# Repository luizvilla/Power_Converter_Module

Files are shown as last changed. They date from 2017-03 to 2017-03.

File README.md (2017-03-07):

# Power_Converter_Module
This repository holds an open-hardware Power Converter Module

Copyright LAAS 2016

This documentation describes Open Hardware and is licensed under the
CERN OHL v. 1.2.

You may redistribute and modify this documentation under the terms of the
CERN OHL v.1.2. (http://ohwr.org/cernohl). This documentation is distributed
WITHOUT ANY EXPRESS OR IMPLIED WARRANTY, INCLUDING OF
MERCHANTABILITY, SATISFACTORY QUALITY AND FITNESS FOR A
PARTICULAR PURPOSE. Please see the CERN OHL v.1.2 for applicable
conditions

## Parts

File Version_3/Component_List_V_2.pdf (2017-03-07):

COMPONENT LIST - DC/DC CONVERTER
Block | Id | Designator | Package | Qty | Designation | Sld.
Support | | P1,P2,P3,P4 | Plastic screws | 4 | -
| | N1,N2,N3,N4 | Plastic nuts | 4 | -
| | M1,M2,M3,M4 | Metal spacers | 4 | -

Driver

1 | DD1 | Diode DO-41 SOD81 Horizontal RM10 | 1 | DIODE
2 | ROH1,ROH2 | Resistor_Horizontal_RM10mm | 2 | 330
3 | CD3 | C_Rect_L7_W2_P5 | 1 | 500n
4 | DR1 | DIP-14_W7.62mm_LongPads | 1 | IRS2186
5 | JPO1,JPO2,JPO3,JPO4 | Pin_Header_Straight_1x02 | 4 | JUMPER
6 | OPT1 | DIP-8_W7.62mm_LongPads | 1 | TLP2631
7 | RM1,RM2 | Resistor_Horizontal_RM10mm | 2 | 2R2
8 | RO1,RO2 | Resistor_Horizontal_RM10mm | 2 | 470
9 | RO3,RO4 | Resistor_Horizontal_RM10mm | 2 | 220
10 | CO1 | C_Rect_L7_W2_P5_fat | 1 | C
11 | CD2,CD1 | C_Rect_L7_W2_P5_fat | 2 | 100n

Feeder

12 | FH2 | 7805 | 1 | 7815
13 | CONH1,CONL1 | BARREL_JACK | 2 BARREL_JACK
14 | DH1,DH2,DL1 | Diode_DO-41_SOD81_Horizontal_RM10 3 | D_Small
15 | FH1,FL1 | 7805 | 2 | 7805
16 | JPF1 | Pin_Header_Straight_1x03 | 1 | JUMPER3
17 | LDH1,LDH2,LDL1 | LED-3MM | 3 | LED
18 | RH1,RH2,RL1 | Resistor_Horizontal_RM10mm | 3 | 10k
19 | CL2,CL1,CH4,CH3,CH2,CH1 | C_Rect_L7_W2_P5_fat | 6 | 1u
20 | PVH1,PVL1 | Potentiometer | 2 | 1M
21 | RiH1,RiL1 | Resistor_TO-220_Vertical | 2 | 0.02
22 | RVH1,RVL1 | Resistor_Horizontal_RM10mm | 2 | 470k
23 | RVH2,RVL2 | Resistor_Horizontal_RM10mm | 2 | 4k7
24 | iA3,iA1,iA2,iA4 | AMC1100 | 4 | AMC1100
25 | C_Rect_L7_W2_P5_fat | 8 | 100nF
Micro | 26 | SH_1,SH2 | ARDUINO_SHIELD_2 | 2

Power

27 | CNH1 | Banana_Jack_2Pin | 1 | HIGH
28 | CNL1 | Banana_Jack_2Pin | 1 | LOW
29 | CPH1,CPL1 | C_Radial_D12.5_L25_P5 | 2 | C
30 | MH1,ML1 | TO-220 | 2 | FDPF39N20
31 | CNDbH1,CNDb1 | Pin_Header_Angled_2x08 | 2 CONN_02X08
32 | L1 | MURATA_Inductor_Big | 1 | INDUCTOR

Measure
ment

C_M8,C_M7,C_M6,C_M5,C_M4,C_ M3,C_M2,C_M1
ARDUINO_SHI
ELD

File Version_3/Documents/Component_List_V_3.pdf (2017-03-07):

COMPONENT LIST - DC/DC CONVERTER
Block | Id | Designator | Package | Qty | Designation
Support | | P1,P2,P3,P4 N1,N2,N3,N4 | Plastic screws Plastic nuts | 4 4 | --
Driver | 1 2 3 4 5 6 7 8 9 10 11 | DD1 ROH1,ROH2 CD3 DR1 JPO1,JPO2,JPO3,JPO4 OPT1 RM1,RM2 RO1,RO2 RO3,RO4 CO1 CD2,CD1 | Diode DO-41 SOD81 Horizontal RM10 Resistor_Horizontal_RM10mm C_Rect_L7_W2_P5 DIP-14_W7.62mm_LongPads Pin_Header_Straight_1x02 DIP-8_W7.62mm_LongPads Resistor_Horizontal_RM10mm Resistor_Horizontal_RM10mm Resistor_Horizontal_RM10mm C_Rect_L7_W2_P5_fat C_Rect_L7_W2_P5_fat | 1 2 1 1 4 1 2 2 2 1 2 | 1N4007 330 500n IRS2186 JUMPER TLP2631 2R2 470 220 100n 100n
Feeder | 12 13 14 15 16 17 18 19 | FH2 CONH1,CONL1 DH1,DH2,DL1 FH1,FL1 JPF1 LDH1,LDH2,LDL1 RH1,RH2,RL1 CL2,CL1,CH4,CH3,CH2,C H1 | 7805 - TO-220 BARREL_JACK Diode_DO-41_SOD81_Horizontal_RM10 7815 - TO-220 Pin_Header_Straight_1x03 LED-3MM Resistor_Horizontal_RM10mm C_Rect_L7_W2_P5_fat | 1 2 3 2 1 3 3 6 | 7815 BARREL_JACK 1N4002 7805 JUMPER3 LED 10k 1u
Measurem ent | 20 21 22 23 24 25 | PVH1,PVL1 RiH1,RiL1 RVH1,RVL1 RVH2,RVL2 iA3,iA1,iA2,iA4 C_M8,C_M7,C_M6,C_M 5,C_M4,C_M3,C_M2,C_ M1 | Potentiometer Resistor_TO-220_Vertical Resistor_Horizontal_RM10mm Resistor_Horizontal_RM10mm AMC1100 C_Rect_L7_W2_P5_fat | 2 2 2 2 4 8 | 1M or 500k 0.02 470k 4k7 AMC1100 100nF
Micro | 26 | Ard_1 SH_1,SH2 | ARDUINO_UNO ARDUINO_SHIELD_2 | 1 2 | ARDUINO ARDUINO_SH IELD
Power | 27 28 29 30 32 | CNH1 CNL1 CPH1,CPL1 MH1,ML1 L1 | Banana_Jack_2Pin Banana_Jack_2Pin C_Radial_D12.5_L25_P5 TO-220 MURATA_Inductor_Big | 1 1 2 2 1 | HIGH LOW C FDPF39N20 INDUCTOR

Debug

33 | P_Test | Borne_test_noir | 14 | T_?
34 | P_Test | Borne_test_rouge | 14 | T_?
PCB | 35 | PCB | PCB | 10 | PCB
Other | 35 | Consummables | - | 1 | -

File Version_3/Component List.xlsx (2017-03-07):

COMPONENT LIST - DC/DC CONVERTER
Block | Id | Designator | Package | Qty | Designation | Sld.
Debug | 1 | TH1,TH2,TH3,TH4,TH5,TH6,TH7,TH8,TH9,TH10,TH11,TH12,TH13,TH14,TH15,TH16,TL1,TL2,TL3,TL4,TL5,TL6,TL7,TL8,TL9,TL10,TL11,TL12 | Measurement_Point_Round-TH_Small | 28 | CONN_01X01
 | 2 | CNDb1 | Pin_Header_Angled_2x08 | 1 | CONN_02X08
 | 3 | SH_1,SH2 | ARDUINO_SHIELD_2 | 2 | ARDUINO_SHIELD
Driver | 4 | DD1 | Diode DO-41 SOD81 Horizontal RM10 | 1 | DIODE
 | 5 | ROH1,ROH2 | Resistor_Horizontal_RM10mm | 2 | 330
 | 6 | CD3 | C_Rect_L7_W2_P5 | 1 | 500n
 | 7 | DR1 | DIP-14_W7.62mm_LongPads | 1 | IRS2186
 | 8 | JPO1,JPO2,JPO3,JPO4 | Pin_Header_Straight_1x02 | 4 | JUMPER
 | 9 | OPT1 | DIP-8_W7.62mm_LongPads | 1 | TLP2631
 | 10 | RM1,RM2 | Resistor_Horizontal_RM10mm | 2 | 2R2
 | 11 | RO1,RO2 | Resistor_Horizontal_RM10mm | 2 | 470
 | 12 | RO3,RO4 | Resistor_Horizontal_RM10mm | 2 | 220
 | 13 | CO1 | C_Rect_L7_W2_P5_fat | 1 | C
 | 14 | C_M8,C_M7,C_M6,C_M5,C_M4,C_M3,C_M2,C_M1 | C_Rect_L7_W2_P5_fat | 8 | 100nF
 | 15 | CD2,CD1 | C_Rect_L7_W2_P5_fat | 2 | 100n
Feeder | 16 | FH2 | 7805 | 1 | 7815
 | 17 | CONH1,CONL1 | BARREL_JACK | 2 | BARREL_JACK
 | 18 | DH1,DH2,DL1 | Diode_DO-41_SOD81_Horizontal_RM10 | 3 | D_Small
 | 19 | FH1,FL1 | 7805 | 2 | 7805
 | 20 | JPF1 | Pin_Header_Straight_1x03 | 1 | JUMPER3
 | 21 | LDH1,LDH2,LDL1 | LED-3MM | 3 | LED
 | 22 | RH1,RH2,RL1 | Resistor_Horizontal_RM10mm | 3 | 10k
 | 23 | CL2,CL1,CH4,CH3,CH2,CH1 | C_Rect_L7_W2_P5_fat | 6 | 1u
Measurement | 24 | PVH1,PVL1 | Potentiometer | 2 | 1M
 | 25 | RiH1,RiL1 | Resistor_TO-220_Vertical | 2 | 0.02
 | 26 | RVH1,RVL1 | Resistor_Horizontal_RM10mm | 2 | 470k
 | 27 | RVH2,RVL2 | Resistor_Horizontal_RM10mm | 2 | 4k7
 | 28 | iA3,iA1,iA2,iA4 | AMC1100 | 4 | AMC1100
Micro | 29 | SH_1,SH2 | ARDUINO_SHIELD_2 | 2 | ARDUINO_SHIELD
Power | 30 | CNH1 | Banana_Jack_2Pin | 1 | HIGH
 | 31 | CNL1 | Banana_Jack_2Pin | 1 | LOW
 | 32 | CPH1,CPL1 | C_Radial_D12.5_L25_P5 | 2 | C
 | 33 | MH1,ML1 | TO-220 | 2 | FDPF39N20
 | 34 | CNDbH1,CNDb1 | Pin_Header_Angled_2x08 | 2 | CONN_02X08
 | 35 | L1 | MURATA_Inductor_Big | 1 | INDUCTOR

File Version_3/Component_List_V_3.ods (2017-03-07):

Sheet: Resumé
Dépense | Description | Valeur
Composants | Tout les composants nécessaires | 700,00 €
Cartes | 6 PCBs | 300,00 €
Consommables | Papier et autres | 50,00 €
 | Total | 1 050,00 €
 | Total par carte | 175,00 €

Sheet: Détails
COMPONENT LIST - DC/DC CONVERTER |  |  |  |  |  | Costs
Block | Id | Designator | Package | Qty | Designation | Price unit | Number | Sub-total
Support |  | P1,P2,P3,P4 | Plastic screws | 4 | - | 10,000 € | 1 | 10,00 €
 |  | N1,N2,N3,N4 | Plastic nuts | 4 | - | 10,000 € | 1 | 10,00 €
Driver | 1 | DD1 | Diode DO-41 SOD81 Horizontal RM10 | 1 | 1N4007 | 0,050 € | 100 | 5,00 €
 | 2 | ROH1,ROH2 | Resistor_Horizontal_RM10mm | 2 | 330 | 0,050 € | 20 | 1,00 €
 | 3 | CD3 | C_Rect_L7_W2_P5 | 1 | 500n | 0,500 € | 20 | 10,00 €
 | 4 | DR1 | DIP-14_W7.62mm_LongPads | 1 | IRS2186 | 0,000 € | 1 | 0,00 €
 | 5 | JPO1,JPO2,JPO3,JPO4 | Pin_Header_Straight_1x02 | 4 | JUMPER | 0,500 € | 6 | 3,00 €
 | 6 | OPT1 | DIP-8_W7.62mm_LongPads | 1 | TLP2631 | 1,500 € | 20 | 30,00 €
 | 7 | RM1,RM2 | Resistor_Horizontal_RM10mm | 2 | 2R2 | 0,055 € | 50 | 2,75 €
 | 8 | RO1,RO2 | Resistor_Horizontal_RM10mm | 2 | 470 | 0,042 € | 20 | 0,84 €
 | 9 | RO3,RO4 | Resistor_Horizontal_RM10mm | 2 | 220 | 0,050 € | 20 | 1,00 €
 | 10 | CO1 | C_Rect_L7_W2_P5_fat | 1 | 100n | 0,200 € | 20 | 4,00 €
 | 11 | CD2,CD1 | C_Rect_L7_W2_P5_fat | 2 | 100n | 0,200 € | 20 | 4,00 €
Feeder | 12 | FH2 | 7805 - TO-220 | 1 | 7815 | 0,300 € | 10 | 3,00 €
 | 13 | CONH1,CONL1 | BARREL_JACK | 2 | BARREL_JACK | 1,500 € | 20 | 30,00 €
 | 14 | DH1,DH2,DL1 | Diode_DO-41_SOD81_Horizontal_RM10 | 3 | 1N4002 | 0,050 € | 100 | 5,00 €
 | 15 | FH1,FL1 | 7815 - TO-220 | 2 | 7805 | 0,300 € | 20 | 6,00 €
 | 16 | JPF1 | Pin_Header_Straight_1x03 | 1 | JUMPER3 | 0,500 € | 6 | 3,00 €
 | 17 | LDH1,LDH2,LDL1 | LED-3MM | 3 | LED | 0,300 € | 30 | 9,00 €
 | 18 | RH1,RH2,RL1 | Resistor_Horizontal_RM10mm | 3 | 10k | 0,050 € | 30 | 1,50 €
 | 19 | CL2,CL1,CH4,CH3,CH2,CH1 | C_Rect_L7_W2_P5_fat | 6 | 1u | 0,500 € | 50 | 25,00 €
Measurement | 20 | PVH1,PVL1 | Potentiometer | 2 | 1M or 500k | 1,000 € | 20 | 20,00 €
 | 21 | RiH1,RiL1 | Resistor_TO-220_Vertical | 2 | 0.02 | 6,000 € | 15 | 90,00 €
 | 22 | RVH1,RVL1 | Resistor_Horizontal_RM10mm | 2 | 470k | 0,050 € | 20 | 1,00 €
 | 23 | RVH2,RVL2 | Resistor_Horizontal_RM10mm | 2 | 4k7 | 0,050 € | 20 | 1,00 €
 | 24 | iA3,iA1,iA2,iA4 | AMC1100 | 4 | AMC1100 | 3,060 € | 30 | 91,80 €
 | 25 | C_M8,C_M7,C_M6,C_M5,C_M4,C_M3,C_M2,C_M1 | C_Rect_L7_W2_P5_fat | 8 | 100nF | 0,200 € | 20 | 4,00 €
Micro |  | Ard_1 | ARDUINO_UNO | 1 | ARDUINO | 5,000 € | 6 | 30,00 €
 | 26 | SH_1,SH2 | ARDUINO_SHIELD_2 | 2 | ARDUINO_SHIELD | 2,000 € | 10 | 20,00 €
Power | 27 | CNH1 | Banana_Jack_2Pin | 1 | HIGH | 4,000 € | 6 | 24,00 €
 | 28 | CNL1 | Banana_Jack_2Pin | 1 | LOW | 4,000 € | 6 | 24,00 €
 | 29 | CPH1,CPL1 | C_Radial_D12.5_L25_P5 | 2 | C | 5,000 € | 20 | 100,00 €
 | 30 | MH1,ML1 | TO-220 | 2 | FDPF39N20 | 1,300 € | 30 | 39,00 €
 | 32 | L1 | MURATA_Inductor_Big | 1 | INDUCTOR | 10,000 € | 6 | 60,00 €
Debug | 33 | P_Test | Borne_test_noir | 14 | T_? | 0,200 € | 100 | 20,00 €
 | 34 | P_Test | Borne_test_rouge | 14 | T_? | 0,200 € | 100 | 20,00 €
PCB | 35 | PCB | PCB | 10 | PCB | 50,000 € | 6 | 300,00 €
Other | 35 | Consummables | - | 1 | - | 50,000 € | 1 | 50,00 €
 |  |  |  |  |  |  | TOTAL | 1 058,89 €
 |  |  |  |  |  |  | TOTAL PAR PCB | 176,48 €

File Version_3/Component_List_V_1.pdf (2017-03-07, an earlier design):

Block | Id | Designator | Package | Qty | Designation
Debug | 1 2 3 | TH1,TH2,TH3,TH4,TH5,TH6,T H7,TH8,TH9,TH10,TH11,TH1 2,TH13,TH14,TH15,TH16,TL1 ,TL2,TL3,TL4,TL5,TL6,TL7,TL8 ,TL9,TL10,TL11,TL12 CNDb1 SH_1,SH2 | Measurement_Point_Round-TH_Small Pin_Header_Angled_2x08 ARDUINO_SHIELD_2 | 28 1 2 | CONN_01X01 CONN_02X08 ARDUINO_SHIELD
Driver | 4 DD1 5 6 7 8 9 10 11 12 13 14 15 | ROH1,ROH2 CD3 DR1 JPO1,JPO2,JPO3,JPO4 OPT1 RM1,RM2 RO1,RO2 RO3,RO4 CO1 C_M8,C_M7,C_M6,C_M5,C_ M4,C_M3,C_M2,C_M1 CD2,CD1 | RM10 Resistor_Horizontal_RM10mm C_Rect_L7_W2_P5 DIP-14_W7.62mm_LongPads Pin_Header_Straight_1x02 DIP-8_W7.62mm_LongPads Resistor_Horizontal_RM10mm Resistor_Horizontal_RM10mm Resistor_Horizontal_RM10mm C_Rect_L7_W2_P5_fat C_Rect_L7_W2_P5_fat C_Rect_L7_W2_P5_fat | 1 DIODE 2 1 1 4 1 2 2 2 1 8 2 | R 500n IRS2186 JUMPER TLP2631 2R2 470 220 C 100nF 100n
Feeder | 17 18 DH1,DH2,DL1 19 20 21 22 23 24 | CONH1,CONL1 FH1,FL1 JPF1 LDH1,LDH2,LDL1 RH1,RH2,RL1 CL2,CL1,CH4,CH3,CH2,CH1 PVH1,PVL1 | BARREL_JACK Diode_DO-41_SOD81_Horizontal_RM10 7805 Pin_Header_Straight_1x03 LED-3MM Resistor_Horizontal_RM10mm C_Rect_L7_W2_P5_fat Potentiometer | 2 3 2 1 3 3 6 2 | BARREL_JACK D_Small 7805 JUMPER3 LED 10k 1u 1M
Measure ment | 25 26 27 28 | RiH1,RiL1 RVH1,RVL1 RVH2,RVL2 iA3,iA1,iA2,iA4 | Resistor_TO-220_Vertical Resistor_Horizontal_RM10mm Resistor_Horizontal_RM10mm AMC1100 | 2 2 2 4 | 0.02 470k 4k7 AMC1100
Micro | 29 30 | SH_1,SH2 CNH1 | ARDUINO_SHIELD_2 Banana_Jack_2Pin | 2 1 | ARDUINO_SHIELD HIGH
Power | 31 32 33 34 35 | CNL1 CPH1,CPL1 MH1,ML1 CNDbH1,CNDb1 L1 | Banana_Jack_2Pin C_Radial_D12.5_L25_P5 TO-220 Pin_Header_Angled_2x08 MURATA_Inductor_Big | 1 2 2 2 1 | LOW C FDPF39N20 CONN_02X08 INDUCTOR

Diode DO-41 SOD81 Horizontal

16 | FH2 | 7805 | 1 | 7815

COMPONENT LIST - DC/DC CONVERTER

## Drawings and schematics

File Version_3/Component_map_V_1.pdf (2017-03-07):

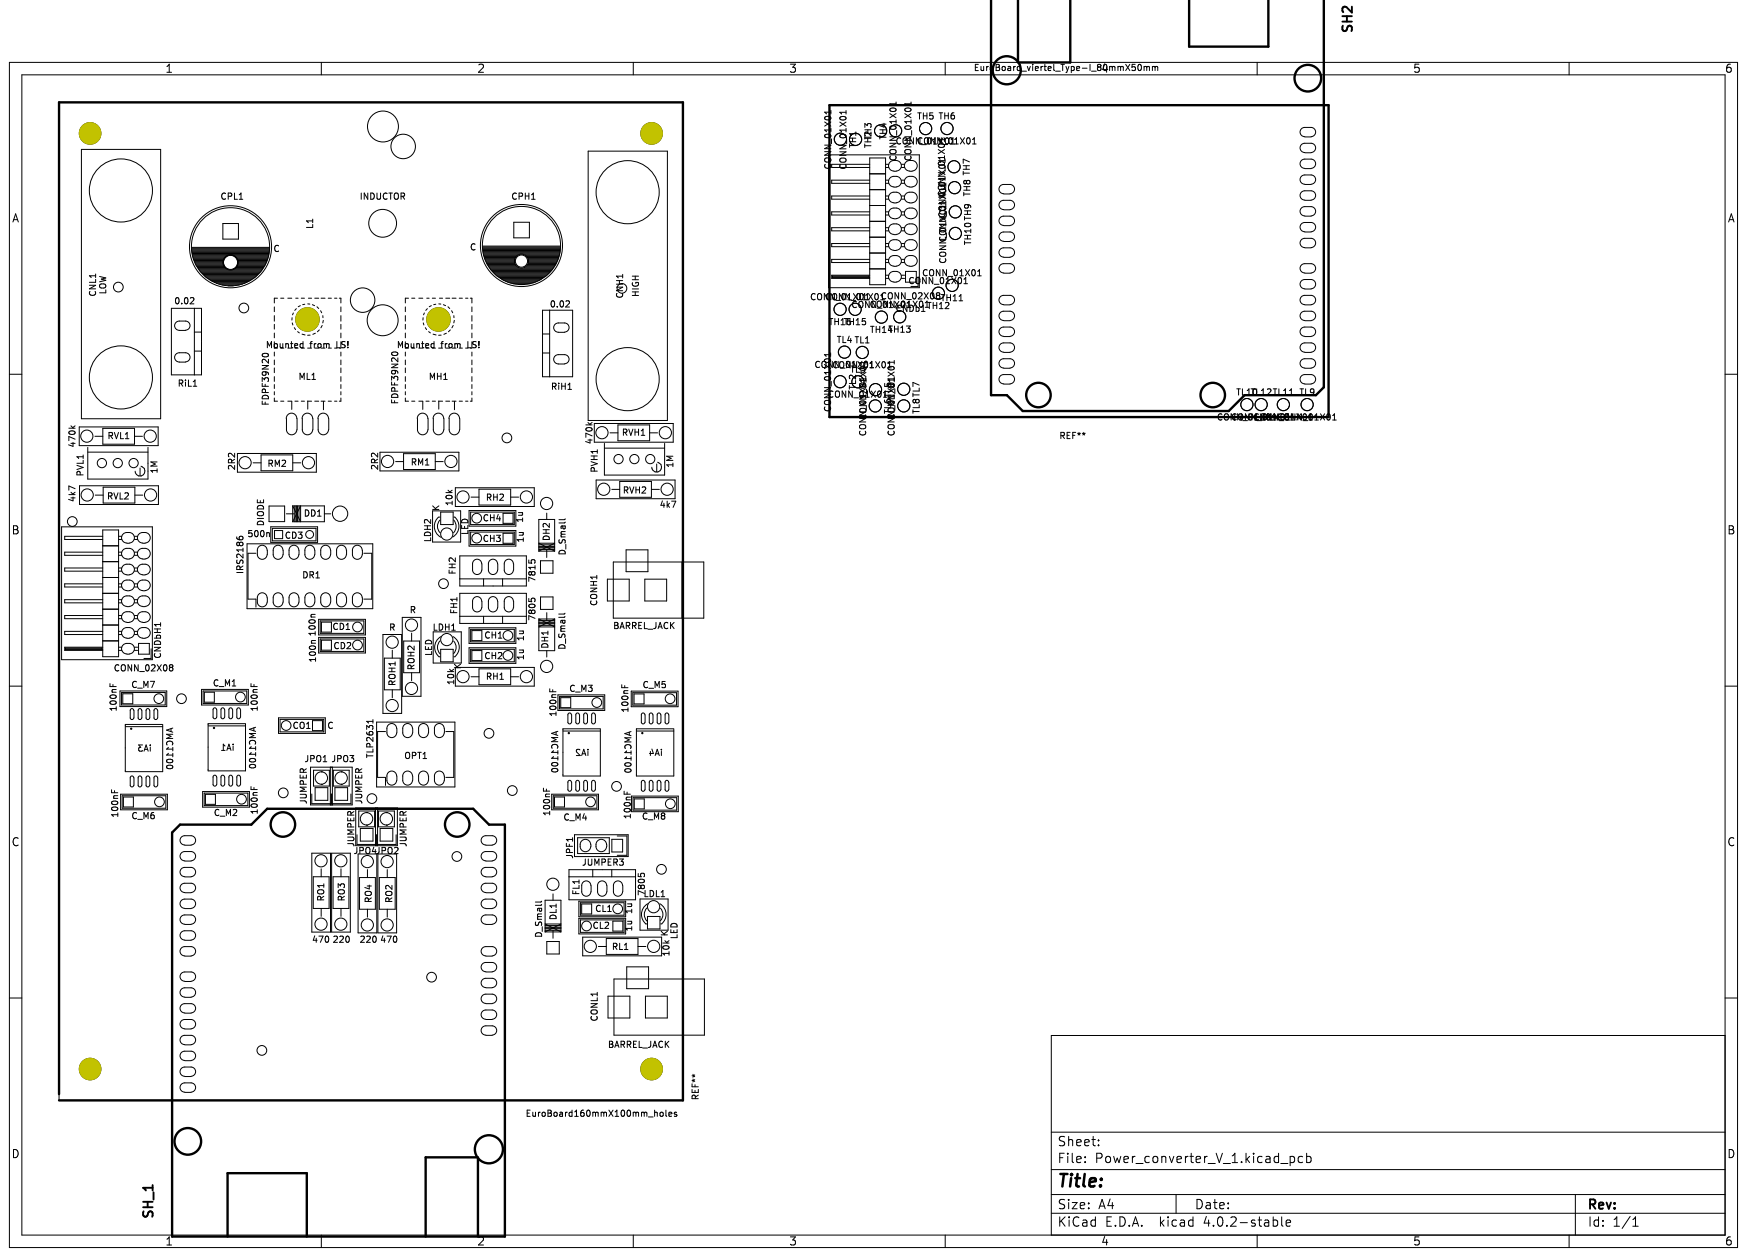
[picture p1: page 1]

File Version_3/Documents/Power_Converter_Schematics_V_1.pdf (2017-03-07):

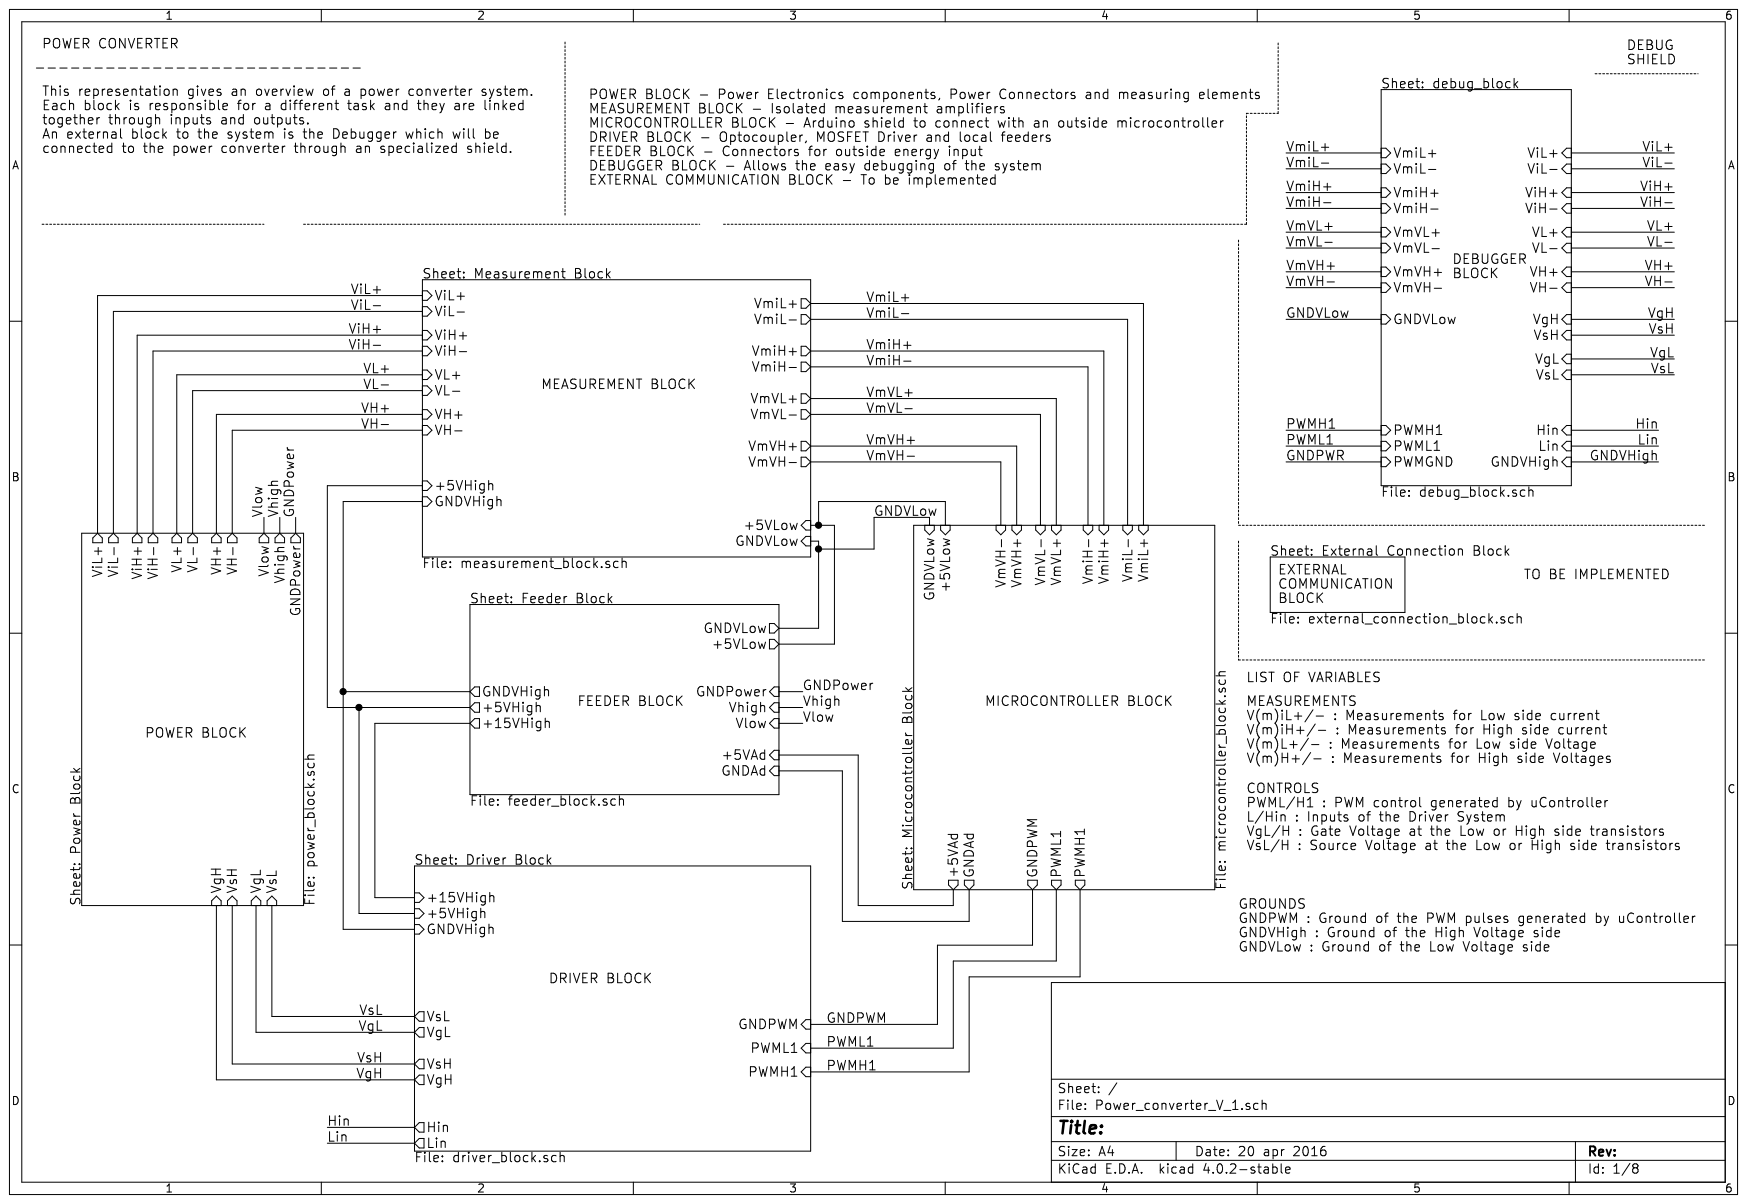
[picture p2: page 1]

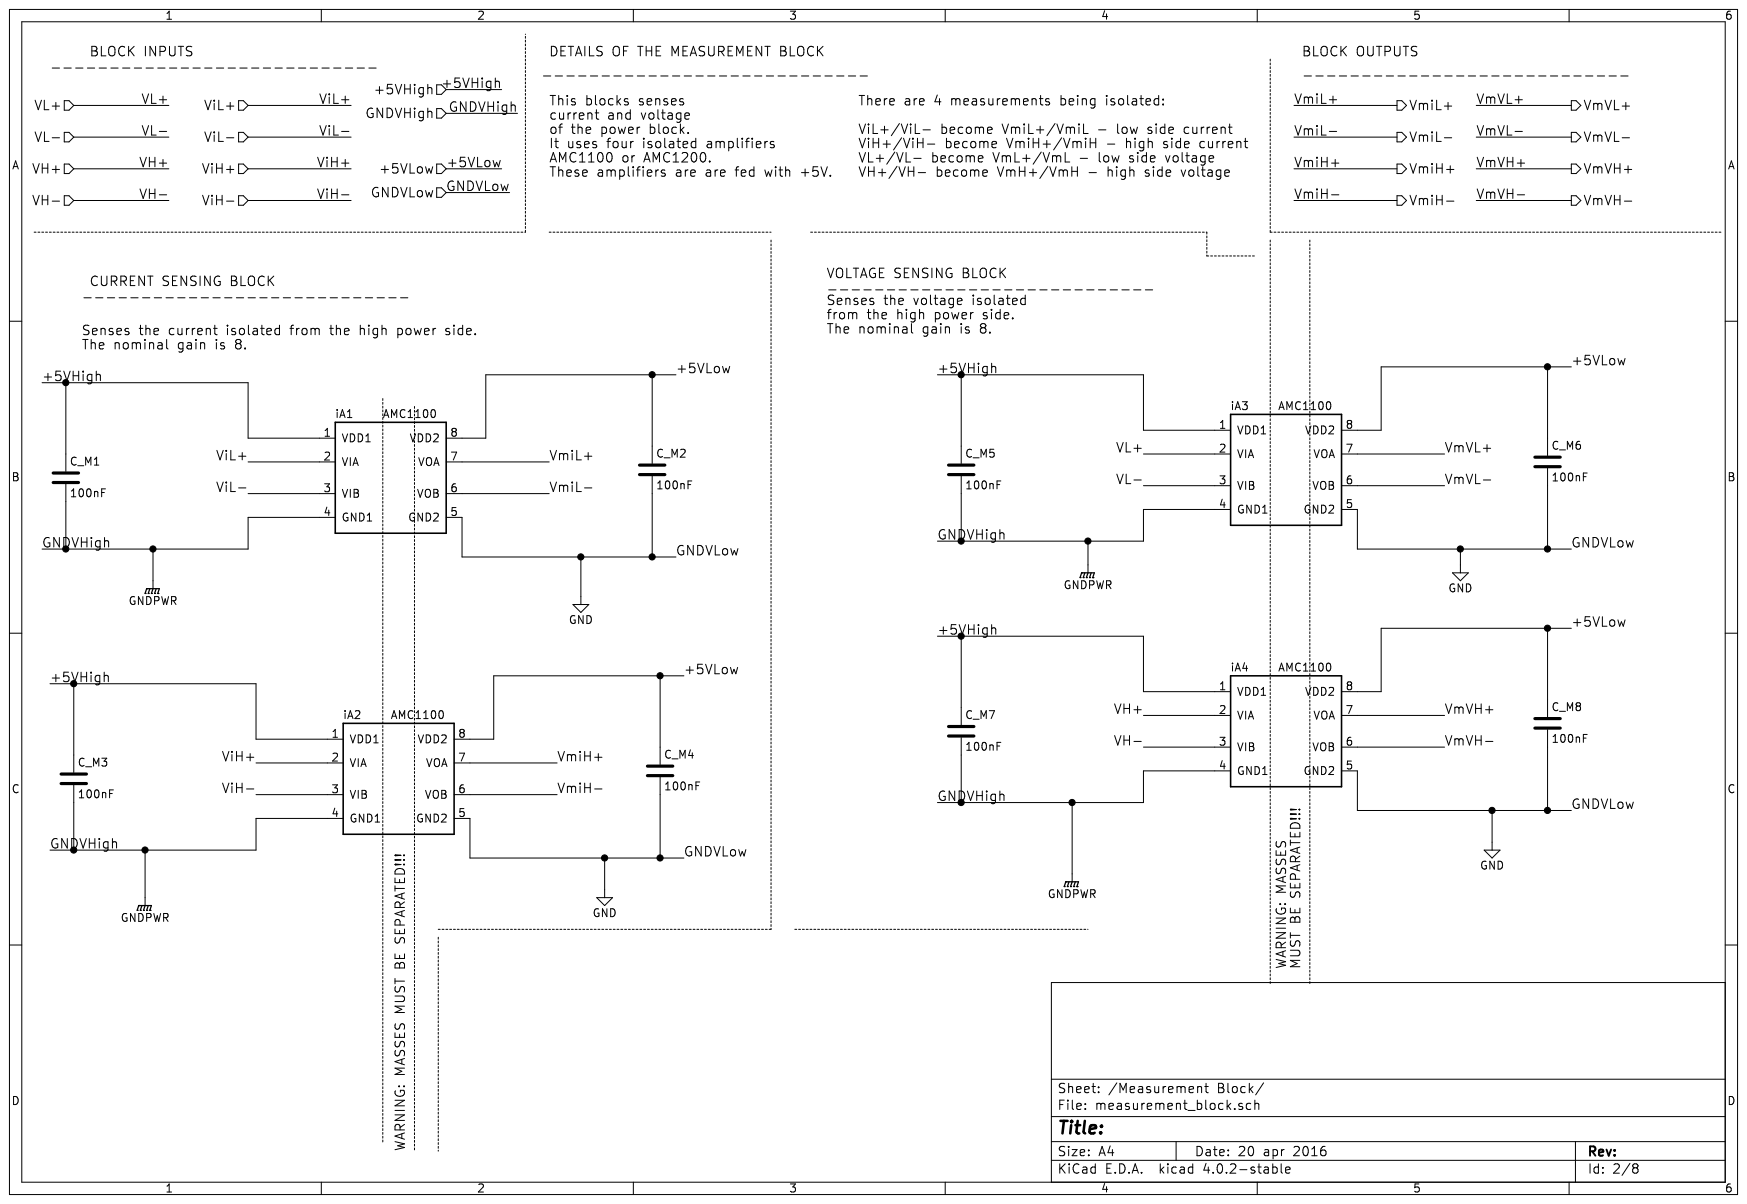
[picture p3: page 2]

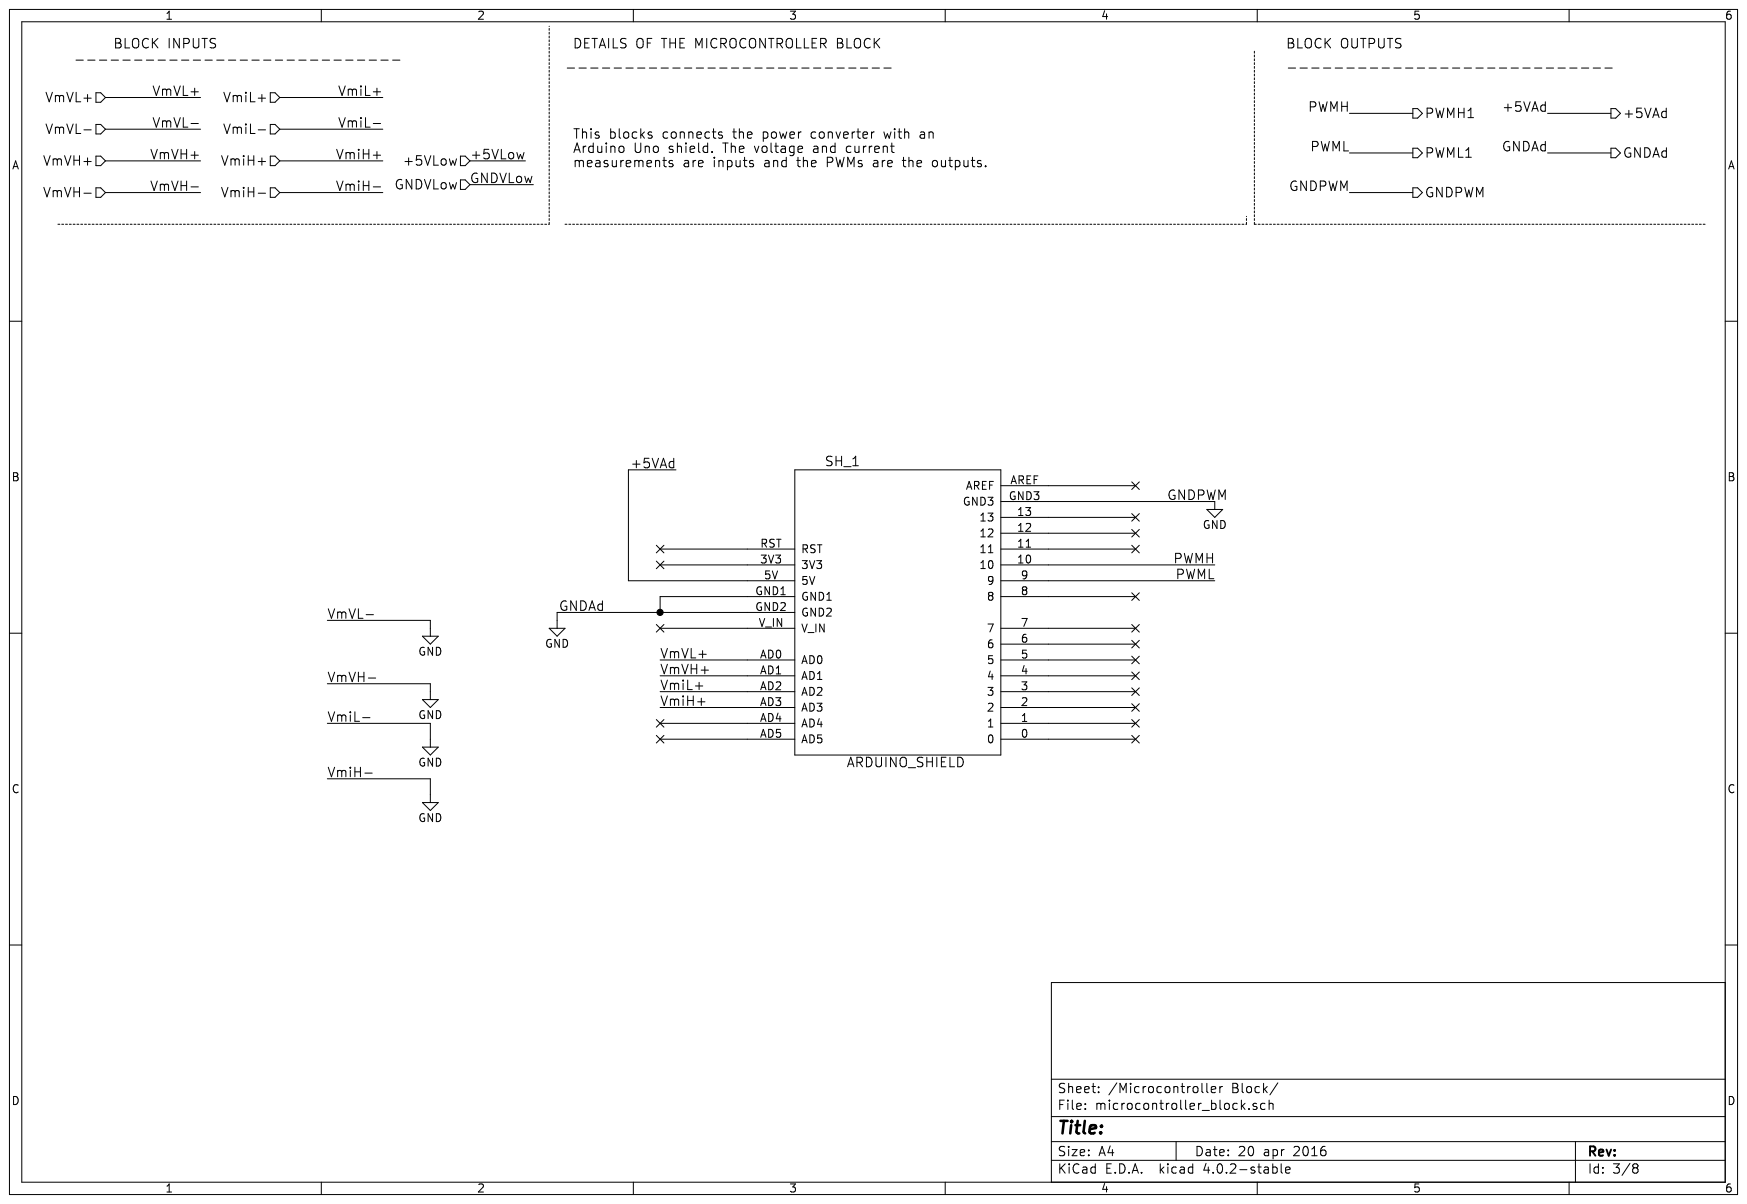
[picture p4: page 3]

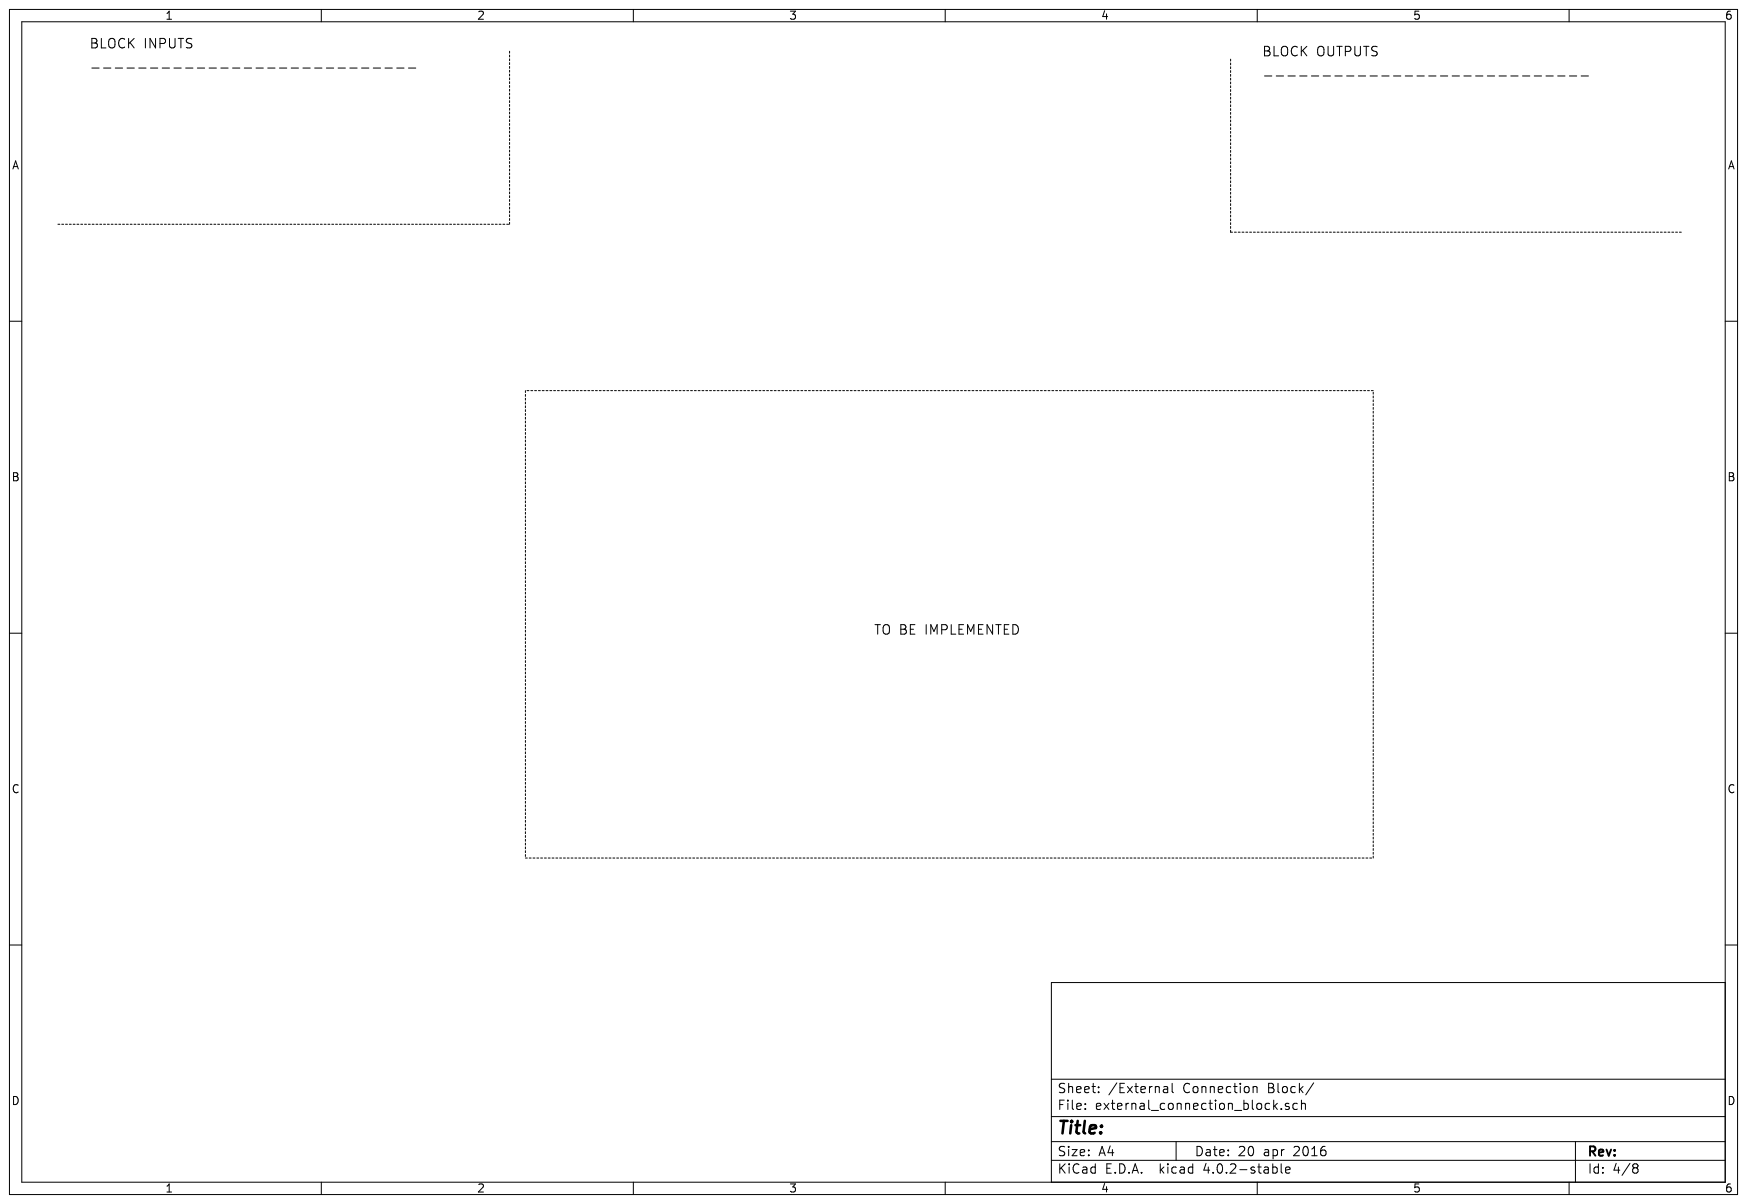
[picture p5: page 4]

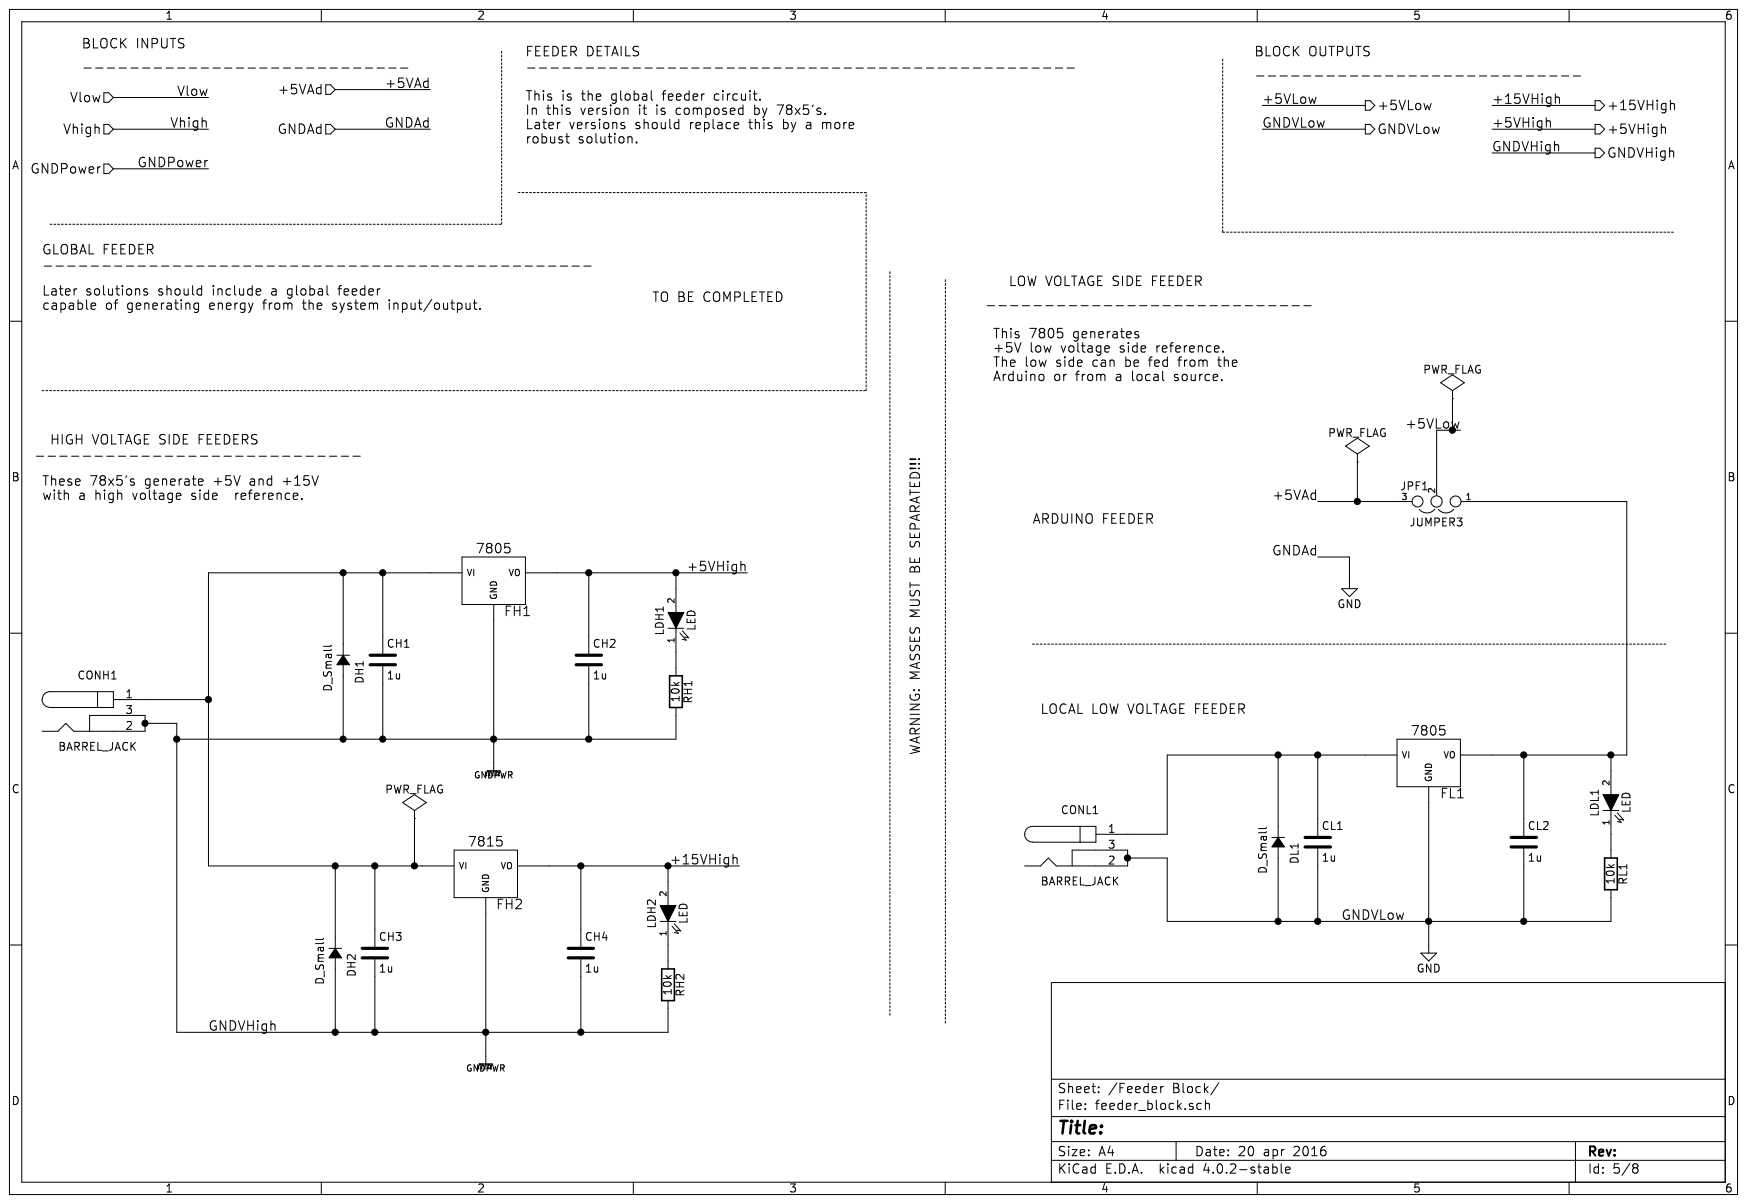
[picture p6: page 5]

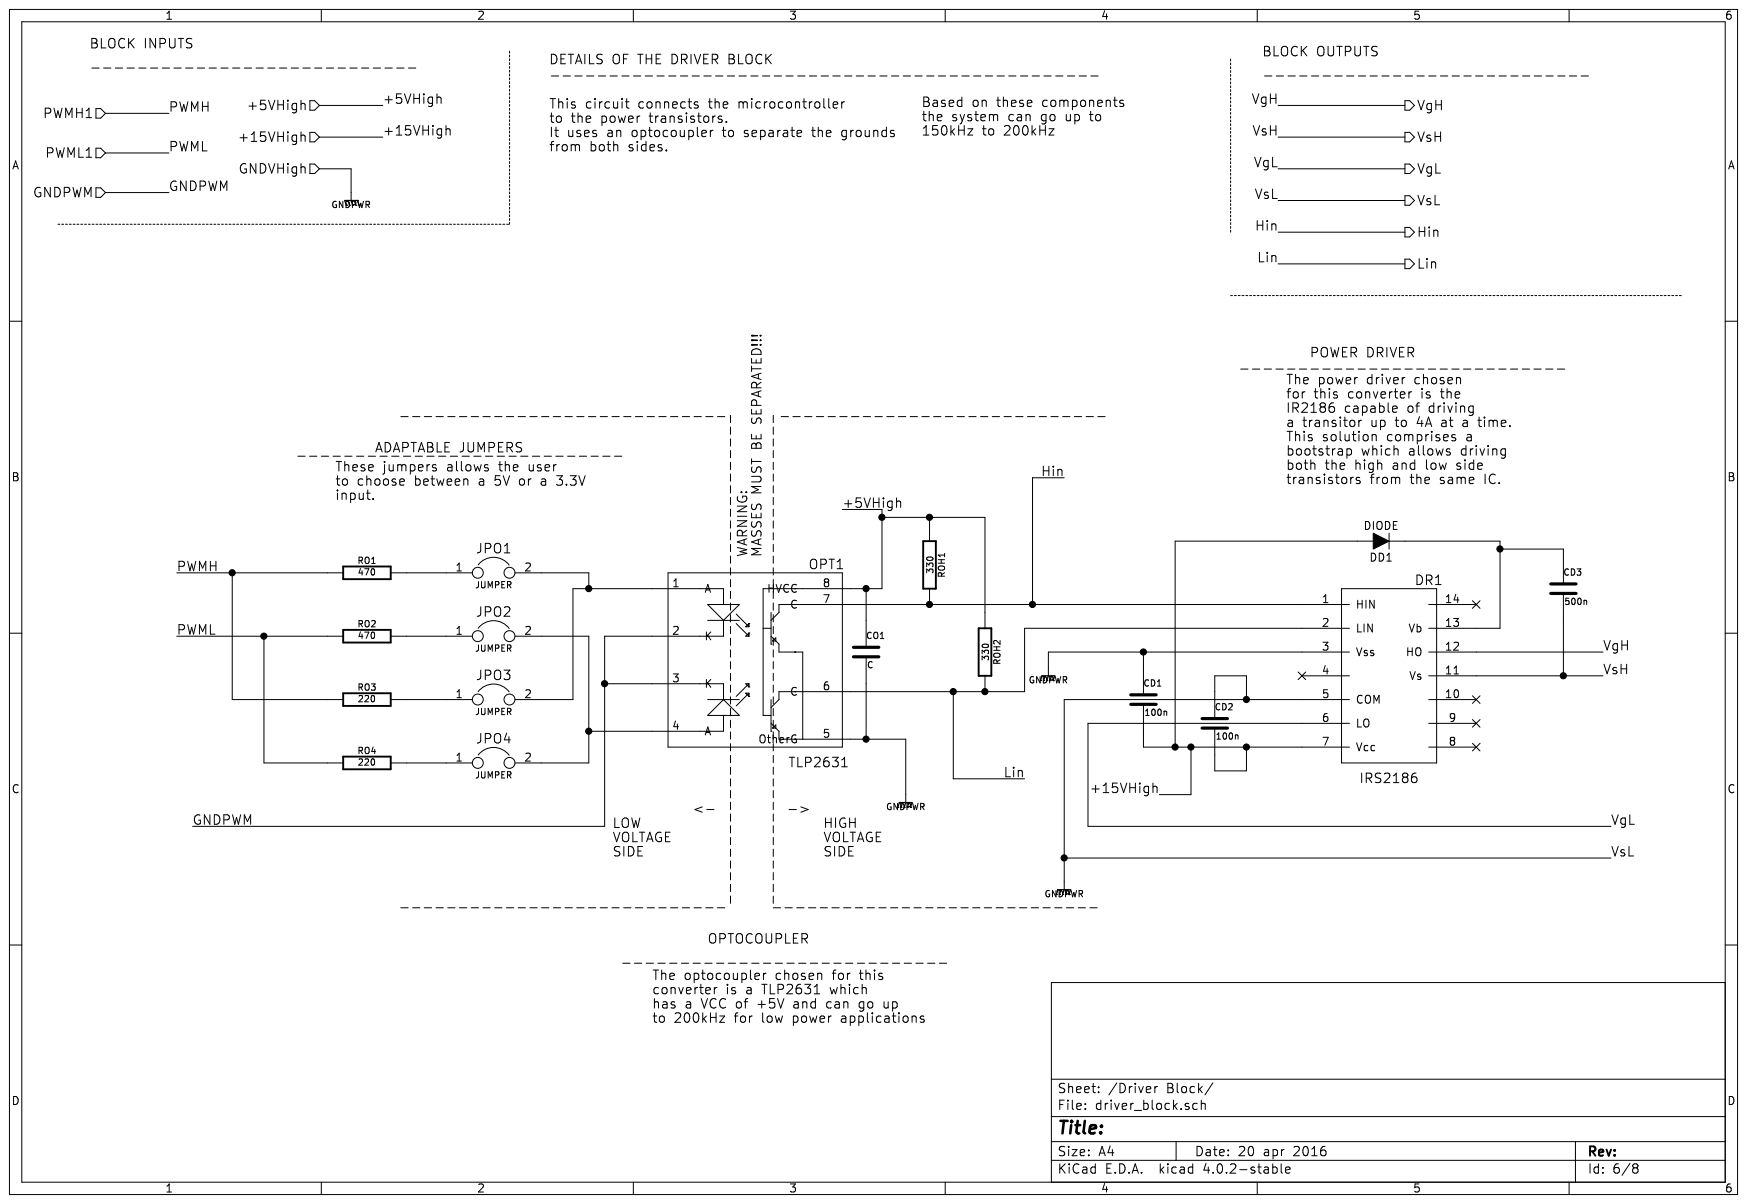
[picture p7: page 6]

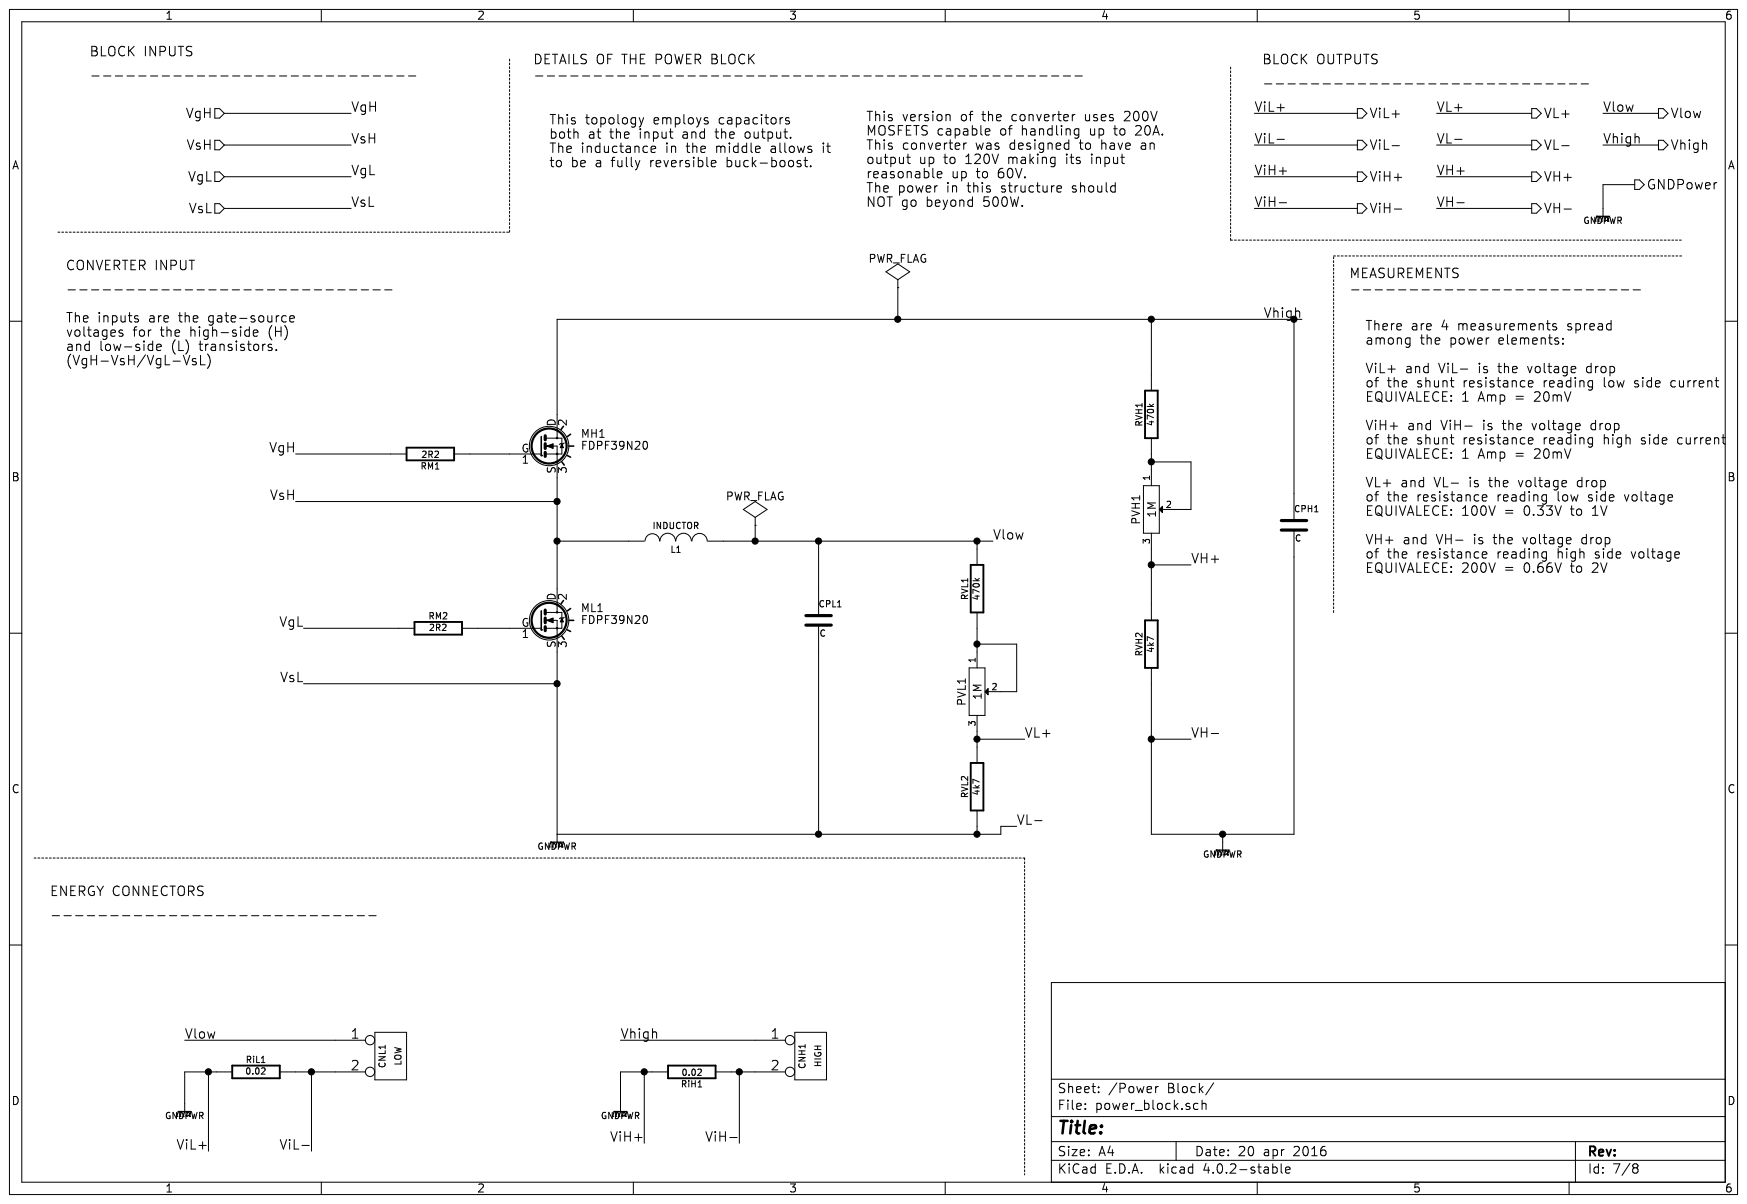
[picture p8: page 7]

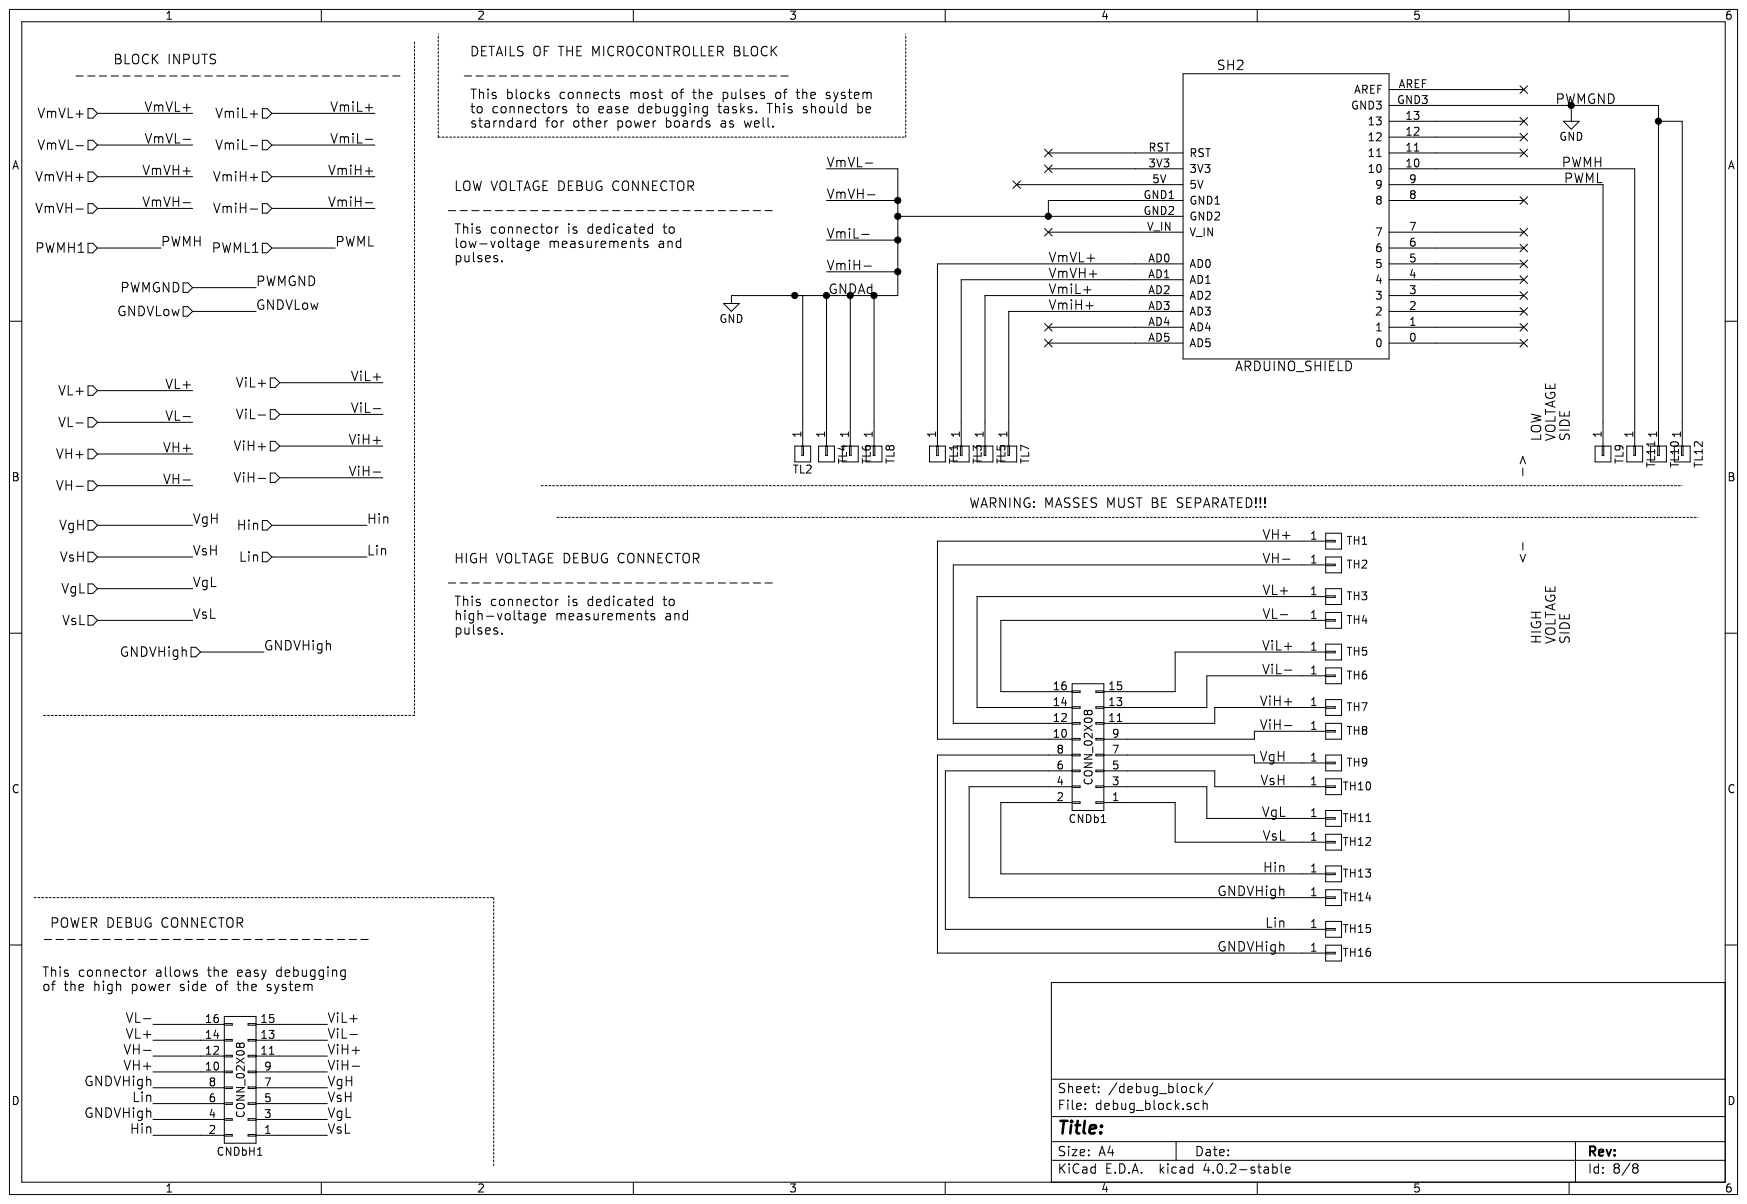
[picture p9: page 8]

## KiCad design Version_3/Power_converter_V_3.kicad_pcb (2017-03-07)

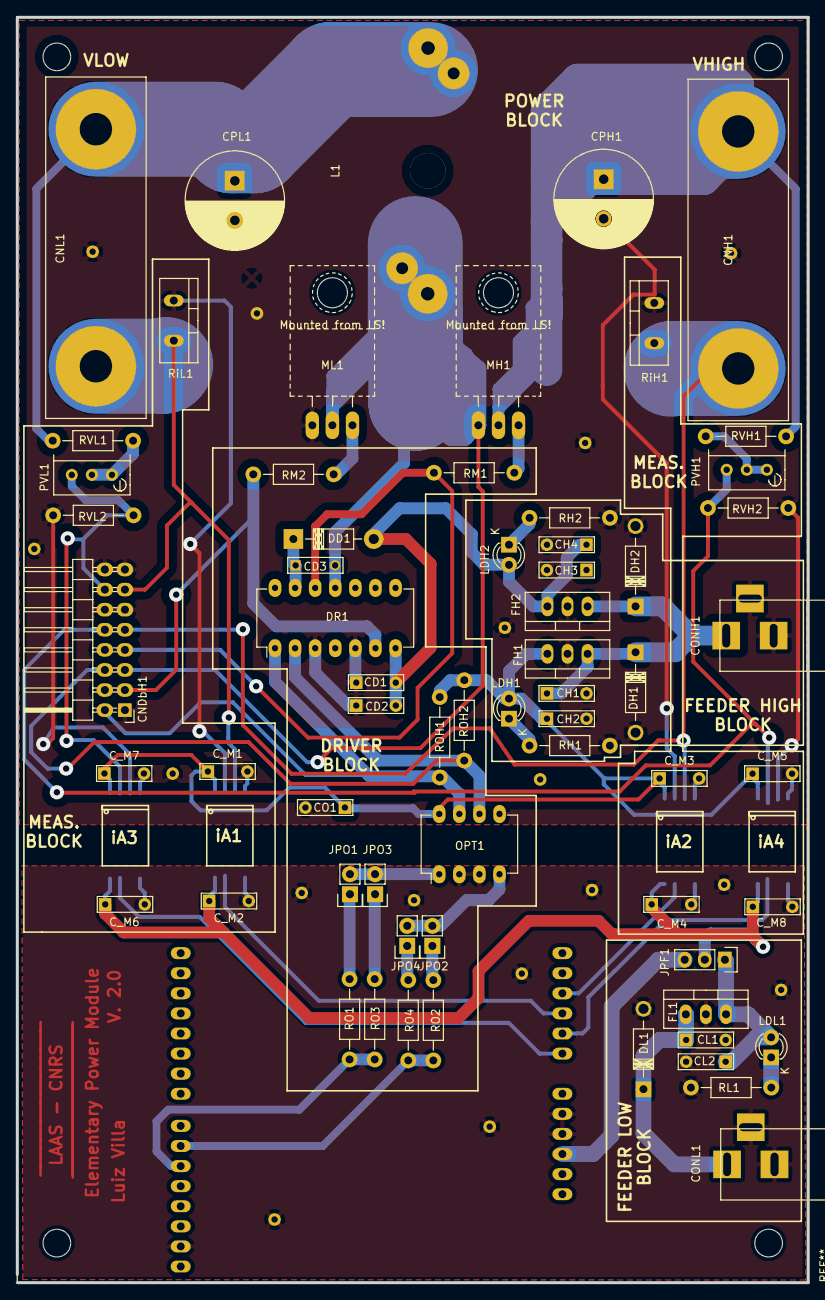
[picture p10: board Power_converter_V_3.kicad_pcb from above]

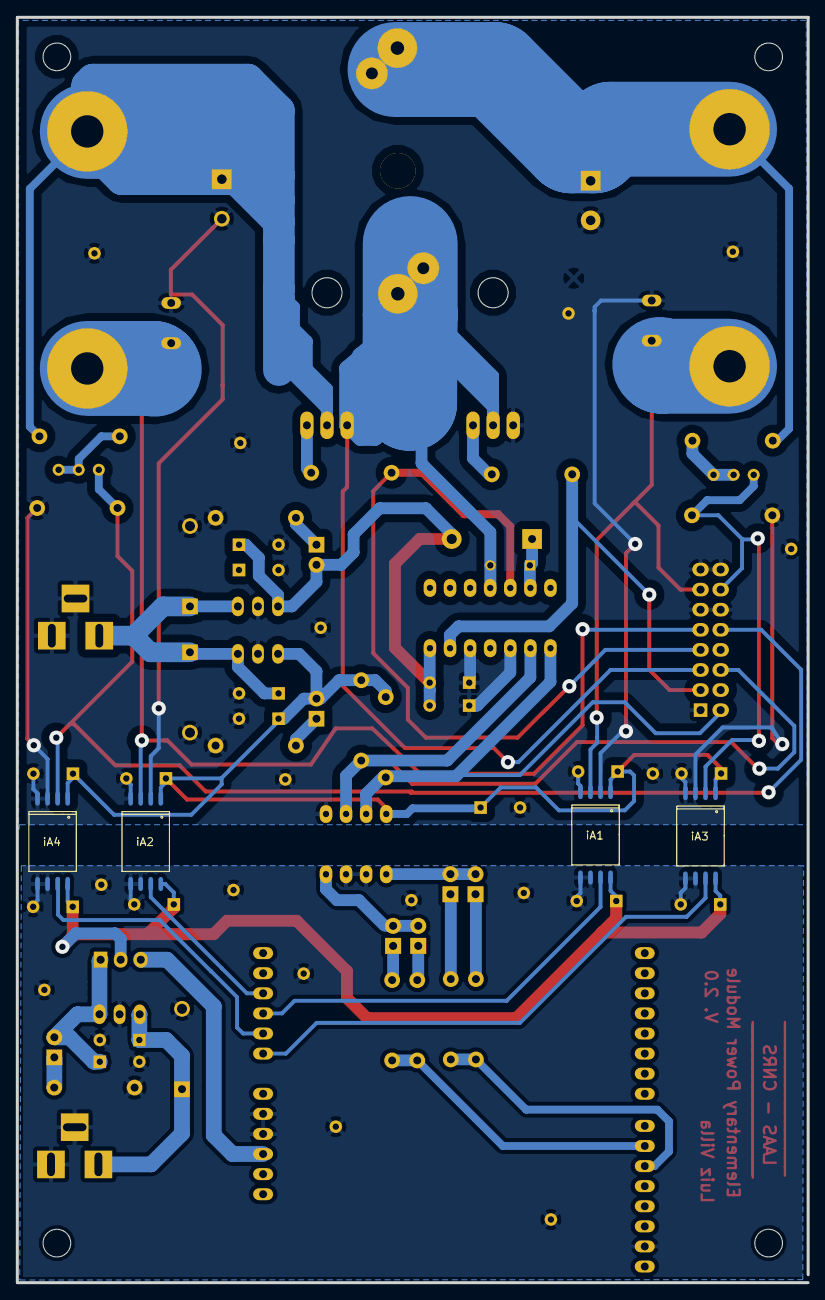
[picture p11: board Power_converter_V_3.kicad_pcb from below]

Board: 2 copper layers, 100.0 x 160.0 mm, 69 parts (4 on the bottom side), 40 nets.

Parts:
CD1, CD2: 100n; C_Rect_L7_W2_P5_fat
CD3: 500n; C_Rect_L7_W2_P5
CH1, CH2, CH3, CH4: 1u; C_Rect_L7_W2_P5_fat
CL1, CL2: 1u; C_Rect_L7_W2_P5_fat
CNDbH1: CONN_02X08; Pin_Header_Angled_2x08_large
CNH1: HIGH; Banana_Jack_2Pin
CNL1: LOW; Banana_Jack_2Pin
CO1: C; C_Rect_L7_W2_P5_fat
CONH1: BARREL_JACK
CONL1: BARREL_JACK
CPH1: C; C_Radial_D12.5_L25_P5
CPL1: C; C_Radial_D12.5_L25_P5
C_M1, C_M2, C_M3, C_M4, C_M5, C_M6, C_M7, C_M8: 100nF; C_Rect_L7_W2_P5_fat
DD1: DIODE; Diode_DO-41_SOD81_Horizontal_RM10
DH1, DH2: D_Small; Diode_DO-41_SOD81_Horizontal_RM10
DL1: D_Small; Diode_DO-41_SOD81_Horizontal_RM10
DR1: IRS2186; DIP-14_W7.62mm_LongPads
FH1: 7805
FH2: 7815; 7805
FL1: 7805
JPF1: JUMPER3; Pin_Header_Straight_1x03
JPO1, JPO2, JPO3, JPO4: JUMPER; Pin_Header_Straight_1x02
L1: INDUCTOR; MURATA_Inductor_Big
LDH1, LDH2: LED; LED-3MM
LDL1: LED; LED-3MM
MH1: FDPF39N20; TO-220_Neutral123_Horizontal_MountedFromLS_LargePads
ML1: FDPF39N20; TO-220_Neutral123_Horizontal_MountedFromLS_LargePads
OPT1: TLP2631; DIP-8_W7.62mm_LongPads
PVH1: 1M; Potentiometer_Bourns_3296W_3-8Zoll_Inline_ScrewUp
PVL1: 1M; Potentiometer_Bourns_3296W_3-8Zoll_Inline_ScrewUp
RH1, RH2: 10k; Resistor_Horizontal_RM10mm
RL1: 10k; Resistor_Horizontal_RM10mm
RM1, RM2: 2R2; Resistor_Horizontal_RM10mm
RO1, RO2: 470; Resistor_Horizontal_RM10mm
RO3, RO4: 220; Resistor_Horizontal_RM10mm
ROH1, ROH2: R; Resistor_Horizontal_RM10mm
RVH1: 470k; Resistor_Horizontal_RM10mm
RVH2: 4k7; Resistor_Horizontal_RM10mm
RVL1: 470k; Resistor_Horizontal_RM10mm
RVL2: 4k7; Resistor_Horizontal_RM10mm
RiH1: 0.02; Resistor_TO-220_Vertical
RiL1: 0.02; Resistor_TO-220_Vertical
SH_1: ARDUINO_SHIELD; ARDUINO_SHIELD_2
iA1, iA2, iA3, iA4: AMC1100

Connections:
/Driver Block/+5VHigh: CH2.1, CO1.1, C_M1.1, C_M3.1, C_M5.1, C_M7.1, FH1.VO, LDH1.2, OPT1.8, ROH1.1, ROH2.1, iA1.1, iA2.1, iA3.1, iA4.1
/Driver Block/+15VHigh: CD1.2, CD2.2, CH4.1, DD1.2, DR1.7, FH2.VO, LDH2.2
/Driver Block/Hin: CNDbH1.2, DR1.1, OPT1.7, ROH1.2
/Driver Block/Lin: CNDbH1.6, DR1.2, OPT1.6, ROH2.2
/Driver Block/PWMH1: RO1.1, RO3.1, SH_1.10
/Driver Block/PWML1: RO2.1, RO4.1, SH_1.9
/Driver Block/VgH: CNDbH1.7, DR1.12, RM1.2
/Driver Block/VgL: CNDbH1.3, DR1.6, RM2.1
/Driver Block/VsH: CD3.2, CNDbH1.5, DR1.11, L1.1, MH1.3, ML1.2
/Feeder Block/+5VAd: JPF1.3, SH_1.5V
/Feeder Block/+5VLow: C_M2.1, C_M4.1, C_M6.1, C_M8.1, JPF1.2, iA1.8, iA2.8, iA3.8, iA4.8
/Feeder Block/Vhigh: CNH1.1, CPH1.1, MH1.2, RVH1.2
/Feeder Block/Vlow: CNL1.1, CPL1.1, L1.2, RVL1.2
/Measurement Block/VH+: CNDbH1.10, PVH1.3, RVH2.2, iA4.2
/Measurement Block/VL+: CNDbH1.14, PVL1.3, RVL2.2, iA3.2
/Measurement Block/ViH-: CNDbH1.9, CNH1.2, RiH1.1, iA2.3
/Measurement Block/ViL-: CNDbH1.13, CNL1.2, RiL1.2, iA1.3
/Measurement Block/VmVH+: SH_1.AD1, iA4.7
/Measurement Block/VmVL+: SH_1.AD0, iA3.7
/Measurement Block/VmiH+: SH_1.AD3, iA2.7
/Measurement Block/VmiL+: SH_1.AD2, iA1.7
/debug_block/GNDVHigh: CNDbH1.4, CNDbH1.8
GND: CD1.1, CD2.1, CH1.2, CH2.2, CH3.2, CH4.2, CL1.2, CL2.2, CNDbH1.1, CNDbH1.11, CNDbH1.12, CNDbH1.15, CNDbH1.16, CO1.2, CONH1.2, CONH1.3, CONL1.2, CONL1.3, CPH1.2, CPL1.2, C_M1.2, C_M2.2, C_M3.2, C_M4.2, C_M5.2, C_M6.2, C_M7.2, C_M8.2, DH1.2, DH2.2, DL1.2, DR1.3, DR1.5, FH1.GND, FH2.GND, FL1.GND, ML1.3, OPT1.2, OPT1.3, OPT1.5, RH1.2, RH2.2, RL1.2, RVH2.1, RVL2.1, RiH1.2, RiL1.1, SH_1.GND1, SH_1.GND2, SH_1.GND3, iA1.2, iA1.4, iA1.5, iA1.6, iA2.2, iA2.4, iA2.5, iA2.6, iA3.3, iA3.4, iA3.5, iA3.6, iA4.3, iA4.4, iA4.5, iA4.6
unnamed: CD3.1, DD1.1, DR1.13
unnamed: CH1.1, CH3.1, CONH1.1, DH1.1, DH2.1, FH1.VI, FH2.VI
unnamed: CL1.1, CONL1.1, DL1.1, FL1.VI
unnamed: CL2.1, FL1.VO, JPF1.1, LDL1.2
unnamed: JPO1.1, RO1.2
unnamed: JPO1.2, JPO3.2, OPT1.1
unnamed: JPO2.1, RO2.2
unnamed: JPO2.2, JPO4.2, OPT1.4
unnamed: JPO3.1, RO3.2
unnamed: JPO4.1, RO4.2
unnamed: LDH1.1, RH1.1
unnamed: LDH2.1, RH2.1
unnamed: LDL1.1, RL1.1
unnamed: MH1.1, RM1.1
unnamed: ML1.1, RM2.2
unnamed: PVH1.1, PVH1.2, RVH1.1
unnamed: PVL1.1, PVL1.2, RVL1.1

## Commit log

2017-03-07 This is the current version of the hardware files
    [Component List.xlsx, Component_List_V_3.ods, Power_converter_V_1.csv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]
2017-04-06 The construction manual for the Power Converter
    This is the constrution manual. It still has errors, but it is a start. The licence needs to be changed still.
